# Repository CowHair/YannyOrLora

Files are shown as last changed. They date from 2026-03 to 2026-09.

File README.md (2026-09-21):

# CanSat Competition 2026 Team Yanny or LoRa 🏆 | 1st in Canada 🇨🇦 and represented Canada at the European Space Agency
*From Eric Hamber Secondary School in Vancouver, BC, Canada*

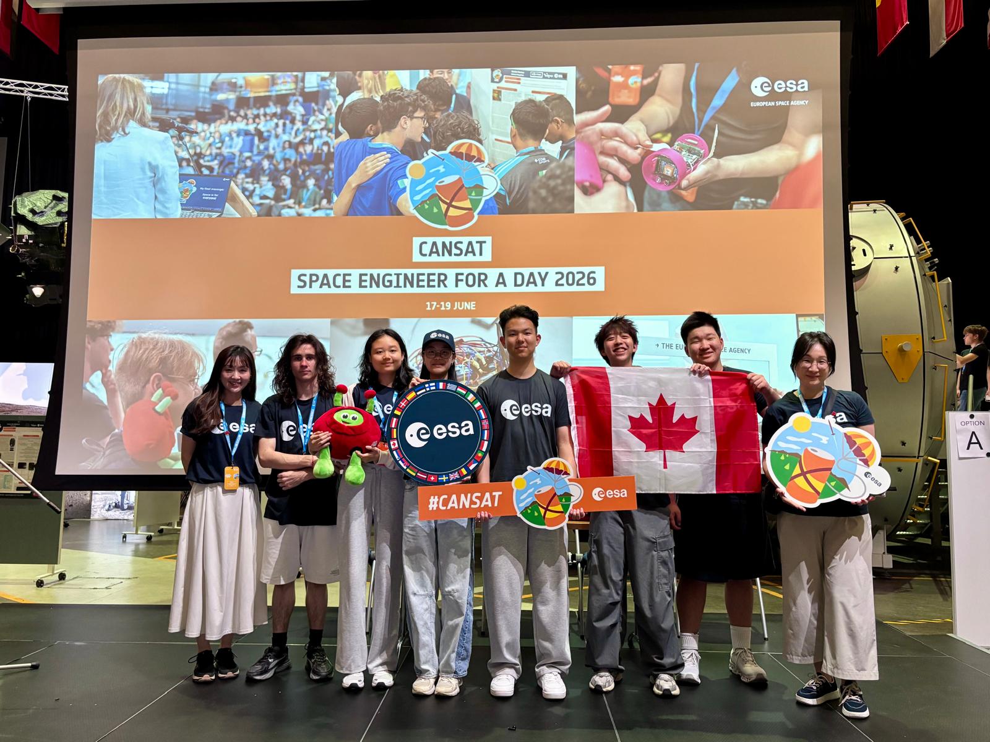
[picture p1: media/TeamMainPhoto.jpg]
Group photo of team


## Team Members

- [Matthew Song](#) - Co-Captain
    - Parachute Design
    - Developing and Testing Landing Gear
- [Asa Liu](#) - Co-Captain
    - Frame Design
    - Mechanical Design
    - Electrical Design
- [Zoey Cheang](https://www.linkedin.com/in/zoey-cheang-855535368/) - Firmware Lead
    - Website Development
    - CanSat Firmware
    - Radio Communication
- [Naiming Zheng](https://www.linkedin.com/in/naiming-z-1a4383371/) - Software Lead
    - Ground Station Software
    - Three-Way Communication Development
- [Bogdan Shkromiuk](https://www.linkedin.com/in/bogdan-shkromiuk-215a08417/) - Hardware Lead
    - Hardware Design
    - CanSat and Radio Device Assembly
    - Frame Design
- [Dora Yuan](https://www.linkedin.com/in/dora-yuan-2a594b307/) - Outreach Lead
    - Outreach Events
    - Designing Landing Gear
    - CanSat Report Main Author

## Project Abstract

The CanSat competition challenges teams to design and build a soda can-sized satellite, launch it to around 1km in altitude, and safely recover telemetry once every second as it descends. Our mission extends the standard telemetry, allowing the CanSat to also act as a relay for a wearable hiker using an SOS device. It listens for signals on a separate radio channel and forwards the hiker's vitals, GPS position, and environmental readings back to the ground station alongside the CanSat's own sensor data, while sending a receipt back to the hiker device so it knows that ground station is aware of its location.

## This Repository

The project is split into the following directories:
 
- [`docs/`](docs/) — our competition website, published live via GitHub Pages at **[https://cowhair.github.io/YannyOrLora]**
- [`firmware/`](firmware/) — Arduino code for all three onboard systems: the CanSat, the ground station, and the SOS device
- [`cad/`](cad/) — 3D models and mechanical design files for the CanSat body and SOS device enclosure
- [`data/`](data/) — telemetry collected during test flights and the competition run
- [`presentations/`](presentations/) — slide decks and reports used during design reviews and the competition

## Mission Overview

The CanSat is launched to around 1km in altitude and descends using a parachute, while continuously transmitting telemetry (temperature, humidity, pressure, altitude, GPS position) to the ground station once per second. Independently, a wearable SOS device carried to simulate a hiker in emergency situation broadcasts a SOS packet with heart rate, GPS position, local temperature/humidity, whenever the button on the device is triggered.

The CanSat acts as the relay between the emergency device and ground station. It listens for the SOS device's signal, caches the most recent emerency data it hears, and piggybacks those fields onto its normal telemetry stream to the ground. The ground station sees both the CanSat's own descent data and the hiker's status in a single feed, without needing separate ground hardware for each link.

## Radio System (Time Sliced Relay Architecture)
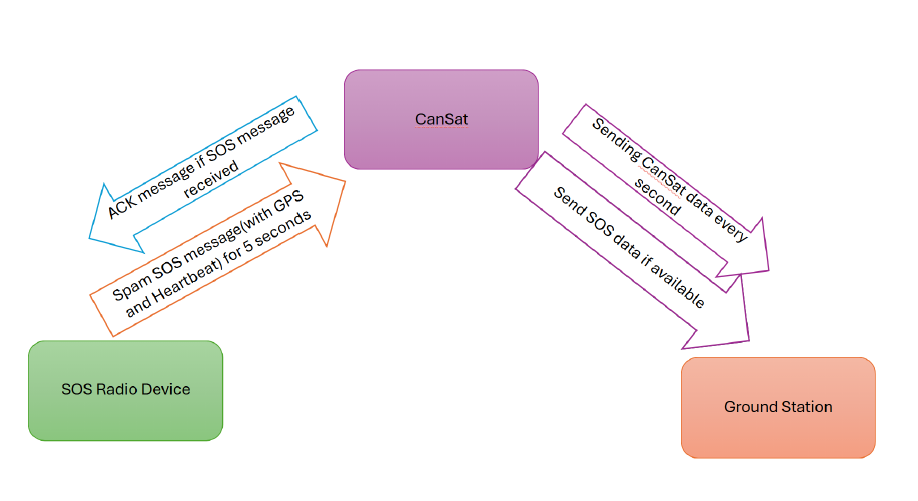
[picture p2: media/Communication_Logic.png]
Communication Logic Image


The onboard radio logic (LoRa, via RadioLib) runs on a strict 1 second frame, split into three phases:

| Phase | Window | Action |
|---|---|---|
| Listen | 0–850 ms | Radio tuned to the SOS device's sync word; any emergency packet received is parsed and cached |
| Transmit | 850 ms–~950 ms | Telemetry is sent to the ground station and an ACK is sent back to the SOS device if time remains in the frame |
| Pad | remainder | GPS and LED housekeeping, holding the frame to exactly 1 second |

Two separate LoRa sync words to keep the two links from colliding on the same channel: one for the CanSat ↔ SOS device link, one for the CanSat → ground link. Cached SOS data expires automatically if no new packet arrives within 10 seconds, so the ground station is never shown stale distress information. ACKs to the SOS device are rate-limited so the CanSat doesn't spend its listen/transmit budget re-acknowledging every frame once contact is established.

## Hardware/Mechanical Design
- Emergency Device Components: BME280, Button, Buzzer, V1 T-Beam ESP32, OLED screen, MAX30102, Toogle Switch, 950kHz Antenna
- CanSat Components: BME280, V1 T-Beam ESP32, LED, Power Switch, 950kHz Antenna
- Designed with FreeCad by Asa Liu and Bogdan Shkromiuk 
<table>
    <tr>
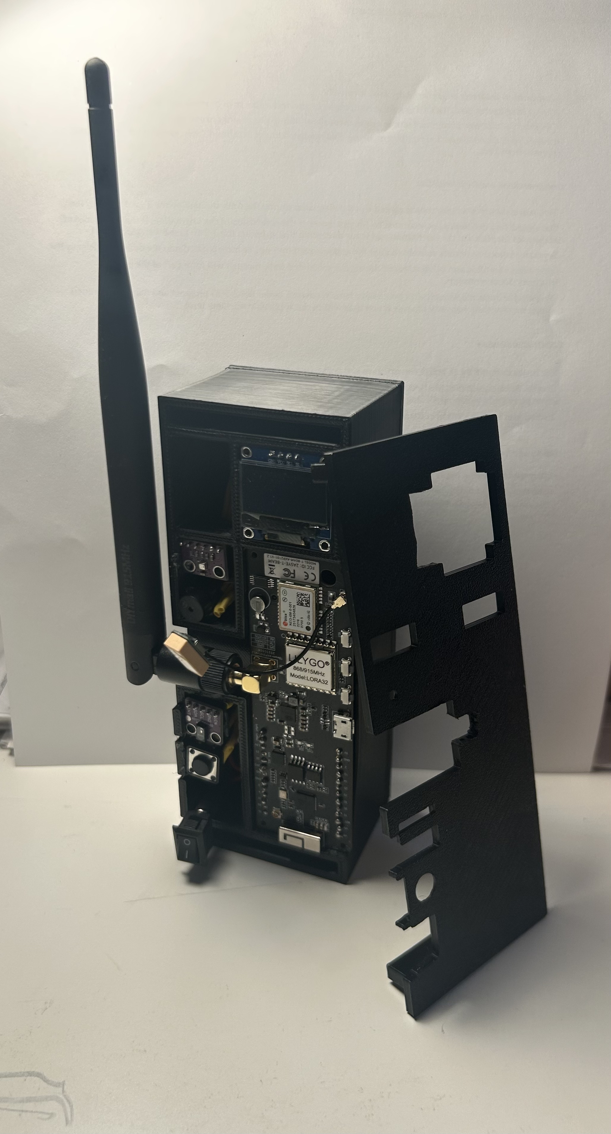
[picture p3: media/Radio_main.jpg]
        <td></td>
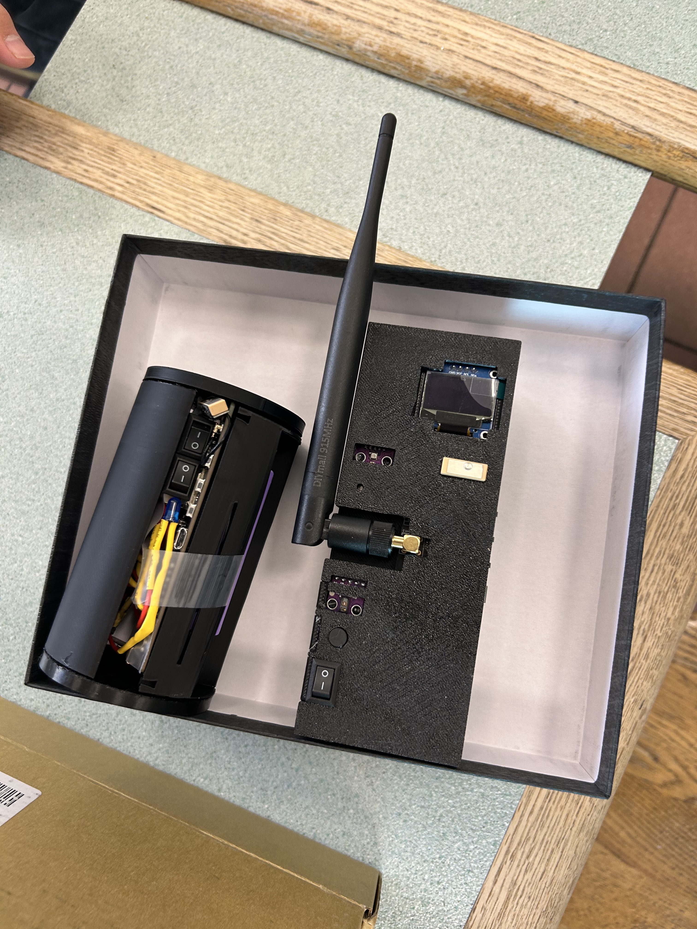
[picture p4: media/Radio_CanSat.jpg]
        <td></td>
    </tr> 
</table>

## Cost Breakdown

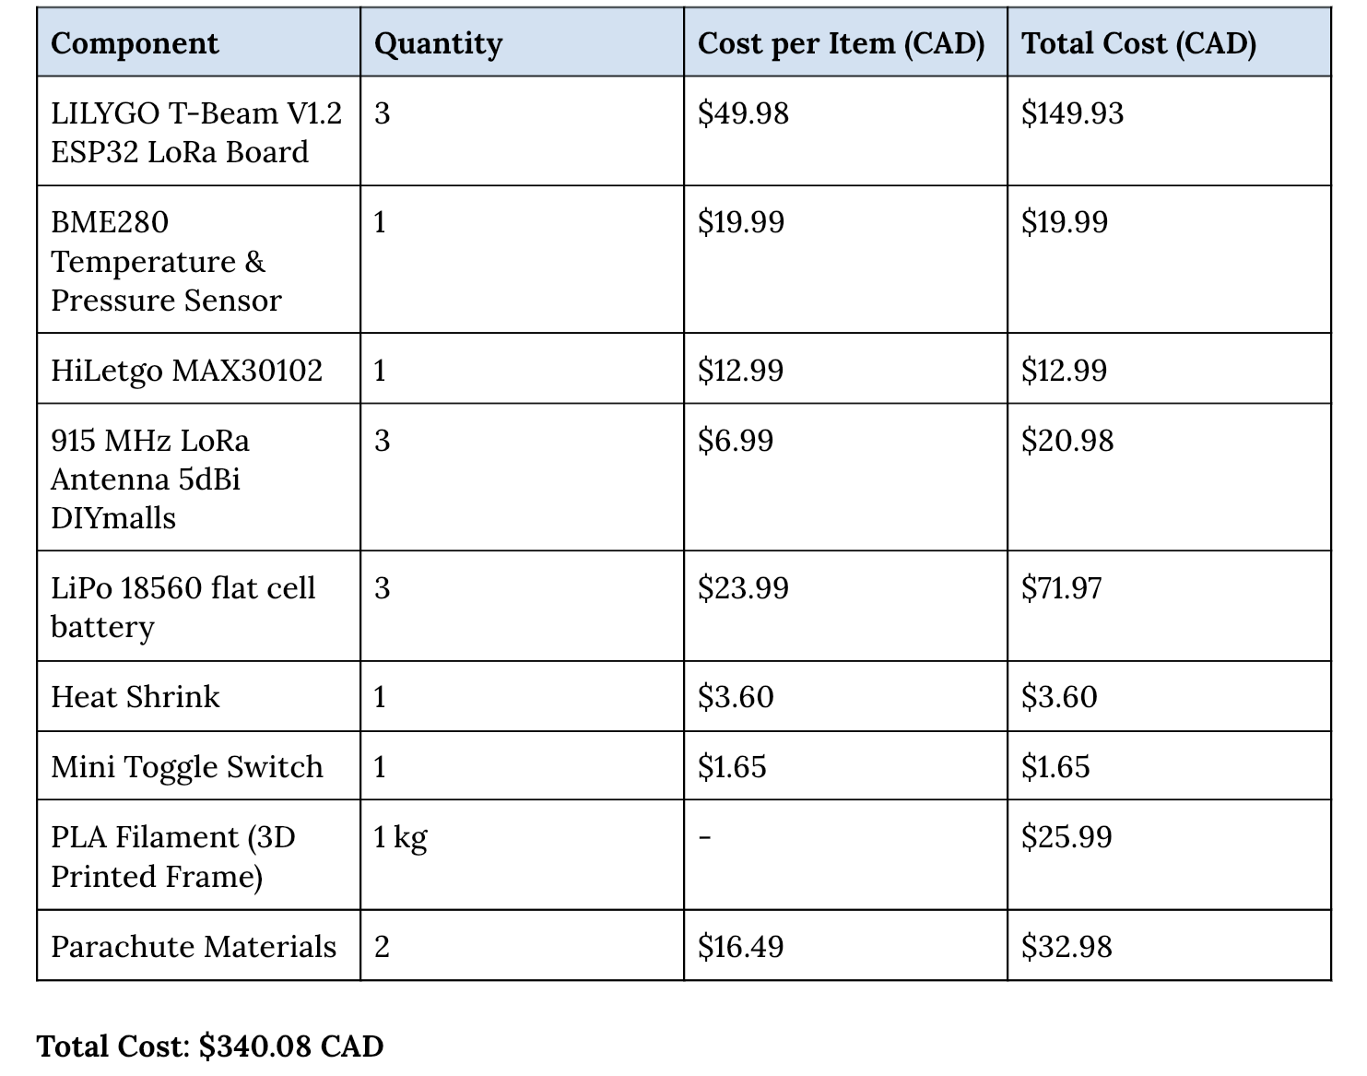
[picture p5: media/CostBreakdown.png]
Table of budget and cost breakdown


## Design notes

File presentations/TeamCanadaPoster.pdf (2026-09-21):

### To measure temperature and pressure once per second

## DESIGN AND COMPONENTS

## PRIMARY MISSION

SECONDARY MISSION To create an SOS radio communication system that includes a hand generator, using the CanSat to extend the range to several kilometers.

## RESULTS

## TESTING

## LESSONS LEARNED

COUNTRY FLAG

# Yanny or LoRa

# CANADA

# CanSat – Space Engineer for a Day 2026

Our CanSat was designed with 3 devices in mind: the ground station, SOS radio device, and the CanSat itself. The LilyGO T-Beam V1.2 ESP32 was chosen as our microcontroller for all 3 devices, for environmental data collection and long-range communication relay.

To build our frames, we used PLA to
maintain a lightweight design for our
CanSat, while our SOS radio device
used nylon as it better protects against external damages. Other components we used includes an OLED display, BME280, and heartbeat sensor on the SOS device to check the user’s health before sending the data to ground station. For our landing system, we used a circular parachute using nylon fabric to prevent ripping during the descent and ensure ease during deployment. Using metal bars and a motor, we also designed a hand crank generator that pairs with our SOS device, ensuring access to the device in remote locations.

After retrieving our CanSat, we noticed water drops from melted snow inside. Fortunately, everything was still functional, and our CanSat did not break.

Our launch conditions were not ideal, with strong winds, a thick cloud cover, and snow. Nonetheless, we successfully received 12 data packets through our LoRa radio system. Halfway through the launch, we lost communication for about 40 seconds and was able to reconnect when it was descending at an altitude of 387.3 metres.

The flight duration was around 150 seconds, the highest recorded altitude reached was 431.7 metres, and the largest distance recorded between the ground station and the CanSat was 599.7m. The descent rate calculated was estimated to be around 5.8m/s. All temperature and pressure data from our BME280 sensor was received successfully in the 12 data packets.

We tested our CanSat extensively, and it was a significant part of our design process.

Firstly, we tested the hardware, including the BME280 sensor, heartbeat clicker, and GPS module. To test, we first had to solder header pins to the LoRa32 board. For some members of our group, it was our first time using Arduino and soldering.

Next, we tested the LoRa communication range by walking in different directions. After confirming a range of around 500–700 meters in dense urban regions with hills, we transferred the BME280 data between the two LoRa32s.

Finally, we tested our parachute landing system using failed frames with weights to find its descent velocity. We walked up a hill and dropped the parachute from 20 meters high. We divided this height by the average time taken for descent to estimate our terminal velocity. To ensure that the parachute would deploy properly under all conditions, we threw it in many different configurations at a variety of linear and rotational speeds.

- The tolerance for PLA has to be a minimum of .25mm and .200 for a perfect fit.
- Designing a PCB would have been a lot for efficient space-wise, removing unnecessary wiring.
- Functionality should be prioritized over aesthetics.

Our secondary mission was very successful. We received 7 packets of data from the SOS radio device, retrieving data on GPS location, temperature, and heart rate.

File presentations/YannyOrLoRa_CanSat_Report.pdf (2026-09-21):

CanSat 2026 | Yanny or LoRa

# Creating an Emergency Radio System Using LoRa Technology

Asa Liu, Matthew Song, Zoey Cheang, Bogdan Shkromiuk, Dora Yuan, Naiming Zheng

Team Name: Yanny or LoRa
School: Eric Hamber Secondary School City: Vancouver, Canada

### ABSTRACT

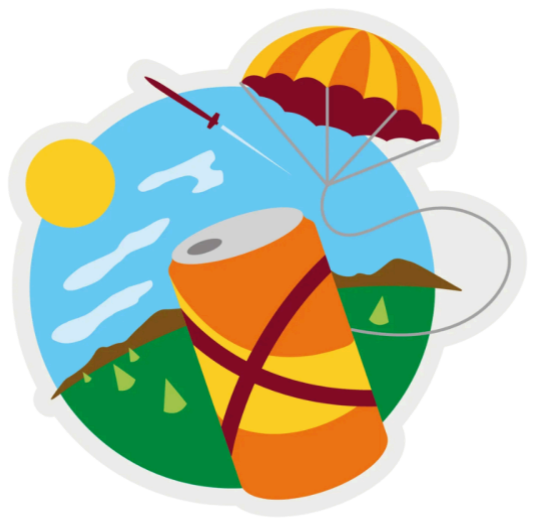
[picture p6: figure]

The advanced CanSat Design Challenge is an annual spring competition where Canadian high school students design a can-sized satellite, which is then launched 1 kilometre by a rocket in Lethbridge, Alberta. Our team, Yanny or LoRa, is composed of 6 high school students from a high school in Vancouver, Canada. Using 3D technology, we constructed a satellite that fulfills two main missions. Our standard primary mission is to collect air pressure, humidity, and temperature data, and to transmit this data through radio back to the ground station. Our secondary mission is to use LoRa (Long Range) technology to create an emergency contact radio system. Our emergency device sends information (specifically SOS signals, heart beat, and GPS location) to the CanSat, which then relays the information back to the ground station. The CanSat allows the message to send through long distances, which we hypothesize to be several kilometres. This store-and-forward system mirrors the communication techniques used in real life satellite systems and is a practical application of aerial LoRa nodes as temporary communication in remote or disaster-affected areas. As the CanSat collects this data, it descends back down using a parachute.

1

### TABLE OF CONTENTS

### 1. INTRODUCTION

### 1.1. Team Mission and Objectives

Our primary mission is to collect air pressure, humidity, and temperature data using a BME280 sensor. This information is collected every second and transmitted through radio to the ground station.

Our secondary mission demonstrates a store-and-forward emergency communication relay system using LoRa radio technology. The concept is that a person in a remote or dangerous location could use a low-power LoRa device to transmit an emergency message to the CanSat, which then relays that message to a home base receiver kilometres away. This has extremely practical effects for a person in a location where they cannot access traditional signal or radio infrastructure. The LoRa technology used for the CanSat extends the effective range of the ground station radio beyond what would otherwise be possible.

Many areas, including Alberta (where we launch our CanSat), have long wildfire seasons that may destroy ground infrastructure and cellular towers. Our CanSat explores the real world problem of finding the minimum viable aerial relay node for emergency communication. Contrary to existing satellites (such as Starlink), our project aims to provide long-range communication without relying on existing infrastructure or

2

large-scale setups. Our aim is to create a useful SOS system that anyone can deploy and use at low cost.

### 1.2. Team Members and Roles

Our team consists of six high school students from Eric Hamber Secondary School, which is a public school in Vancouver, Canada.

Asa Liu (co-captain)
Asa Liu is a grade 11 student at Eric Hamber Secondary who plans on pursuing a future in becoming an astronaut. He has an incredible drive towards building new projects centered around controlled movement. Asa’s background includes many Arduino-based projects and participating in physics competitions. His role in the team is planning and organizing the CanSat build. He is also leading the secondary mission (LoRa development) and designing the frame + hardware systems.

Matthew Song (co-captain)
Matthew Song is a grade 11 student who plans to pursue aerospace or mechanical engineering at university. He has a strong interest in engineering and safety design, and is currently working on an engineering project centered around improving the protective performance of football helmets. Besides academics, he also enjoys golfing and watching football. On the team, Matthew is responsible for developing and testing the landing gear. He will also run meetings and make sure that everyone is on pace to finish.

Zoey Cheang
Zoey Cheang is a grade 12 student who plans on pursuing computer science in university and work in the cybersecurity industry in the future. She has participated in multiple Capture The Flag competitions and is working toward building a strong foundation in networking protocols. She is comfortable coding with Python, C++ and Java. Zoey will be focusing on working on the three-way communication LoRa protocol, electronics hardware, and creating a website for the team.

Naiming Zheng
Naiming Zheng is a grade 11 student at Eric Hamber Secondary School who plans to pursue computer science at university. He is proficient in Python and Java, and he is currently trying to learn Rust to get a deeper understanding of system programming and memory safety. Naiming is also in Eric Hamber’s cybersecurity club and competes in Capture the Flag Competitions. Naiming is responsible for the software side of the primary mission, focusing on sensor data processing and controller logic.

3

Dora Yuan
Dora Yuan is a grade 11 student at Eric Hamber who is passionate about engineering, and is planning on pursuing it in university. She has a strong background in physics, is proficient in Python, and is currently expanding her knowledge on electronics and CAD. On the team, she will be leading the outreach, as well as working on the CanSat landing gear. She is the main writer of this report.

Bogdan Shkromiuk
Bogdan Shkromiuk is a grade 12 student at Eric Hamber who plans to pursue electronic engineering at university. He has a strong physics background and is experienced with 3D modeling, printing, and soldering. He will use these skills to build the CanSat frame and help with electronics.

TEACHER: Mark Lam
Mark Lam is this team’s teacher and an Eric Hamber alumnus who graduated from UBC with a degree in physics. At Eric Hamber Secondary, he teaches many physics courses, including both AP Physics C classes. He has been doing CanSat with his students for many years, on top of supporting his class in various other physics events and opportunities.

### 2. CANSAT DESCRIPTION

### 2.1. Mission Overview (Main Components)

LilyGO T-Beam V1.2
Figure 1: LilyGO T-Beam

4

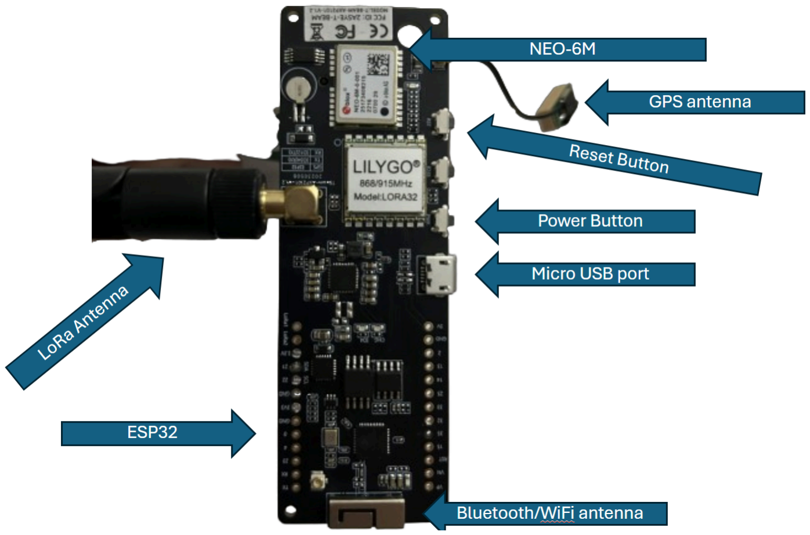
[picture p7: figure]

There are three main devices in our missions, CanSat, ground station, and SOS radio device. Our central component for all three devices is a LilyGO T-Beam V1.2. This contains a microcontroller, a LoRa module, a GPS module, an antenna, and a built-in battery connector.

Microcontroller
The microcontroller we are using is an ESP32. The board is mounted in the middle platform of the CanSat structure using plastic layers and screws. We have also used standoffs to prevent electrical contact between circuit board and base to prevent electrical short circuits.

LoRa Module
The LoRa module we are using is SX1276. It is designed specifically for long range, low-powered wireless communication, which greatly suits our missions. In our missions, it will be operated in the 915MHz ISM band.

GPS module
We are using the u-box NEO-6M GPS module. It provides geographic coordinates and altitude, helping us to track the CanSat location.

Antenna
We are using a 915 MHz LoRa antenna to match the frequency we are using for our LoRa transmitter. The antenna is mounted with the SMA male of the T-Beam module.

Battery
We will be using the LiPo 18650 flat-top cell 3.7V battery. It provides enough voltage to power the ESP32 and other sensors. The battery is housed in the integrated holder on the underside of the T-Beam. It is rechargeable via the micro-USB port integrated directly onto the T-Beam board.

CanSat
The main parts of our CanSat consists of a LilyGO T-Beam V1.2 mentioned above, a LED, a sensor, a power switch, and a parachute.

Figure 2: Our CanSat

5

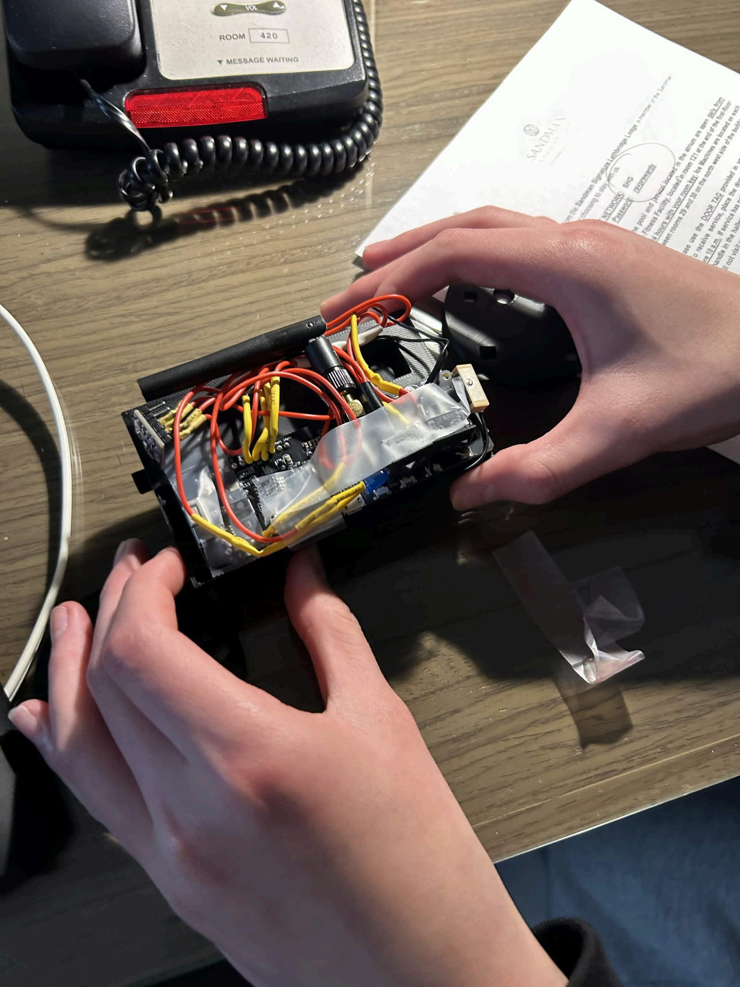
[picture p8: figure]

Sensor
We are using a BME280 sensor, which tracks temperature, air pressure, and humidity. The sensors will be mounted on the same platform as the microcontroller. There will be holes to allow for air to flow in without endangering the sensor.

LED
The LED is used as an indicator when the CanSat is powered on. It is clearly visible on the side of our CanSat.

Power Switch
The power switch is clearly visible on the side of our CanSat, alongside with the LED to power on the CanSat.

Parachute
Our circular parachute system is attached to the top of the CanSat structure. The attachment point is reinforced to withstand the forces experienced when the parachute deploys. The parachute lines connect to the top cap so that the CanSat remains upright during descent, ensuring the antenna maintains good communication with the ground station. More information about the parachute can be found below, in 2.5. Recovery System.

SOS radio device

6

The main components of our SOS radio device consists of a BME280, a heartbeat sensor, a buzzer, a power switch, a LilyGO T-Beam V.1.2 (mentioned above), SOS button, and an OLED screen.

Figure 3: Radio device

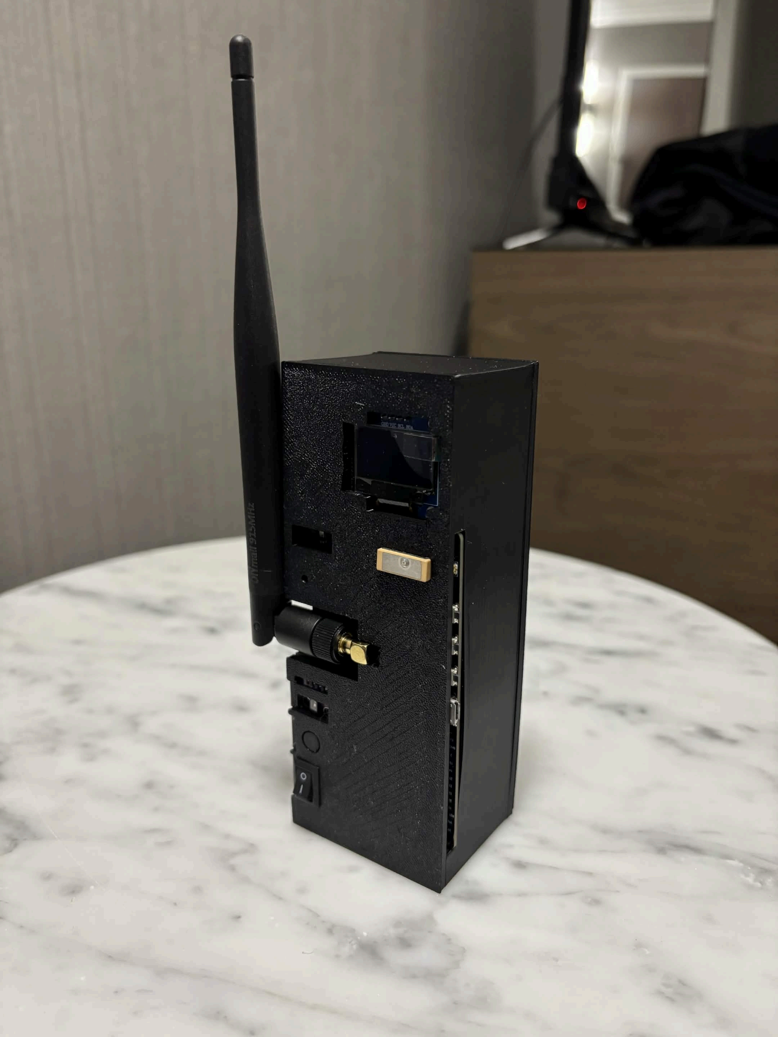
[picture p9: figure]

OLED Screen
The OLED screen displays BME280 data (Altitude, Humidity, Pressure, Temperature), GPS location, and heartbeat (in BPM). When an SOS message is sent, the OLED screen will indicate to the user that the message is being sent. When the SOS radio device receives an ACK message from the CanSat, the OLED screen will display to the user that the message is sent successfully.

BME280
The BME280 sensor allows us to collect temperature, humidity, altitude, and air pressure allowing the ground station to see the surrounding conditions of the SOS Radio.

Heartbeat Sensor
Using a simplistic 3d frame design we are able to collect the heart rate (bpm) of any user that puts their finger on top of the carefully designed frame that rests on top of the sensor. When measuring your heart rate the OLED screen automatically switches to heart reading mode and displays your bpm in big visible numbers.

LILYGO T-Beam v1.2
The LoRa32 microcontroller is the core of the SOS device. It is connected to all the parts and processes both sensors while communicating with the CanSat.

Buzzer

7

The buzzer beats to the BPM and is only active when a finger is on the sensor.

Power Switch
Turns on/off the SOS Radio.

SOS Button
Sends an SOS signal to the CanSat when double-clicked. Double-clicking again cancels the SOS. Sends the GPS location and the heartbeat of the radio device user.

### 2.2. Structural Design (Frame)

For the final frame design, we went with a 4-part frame with 2 body parts along with a top lid and bottom lid.

Figure 4: Frame

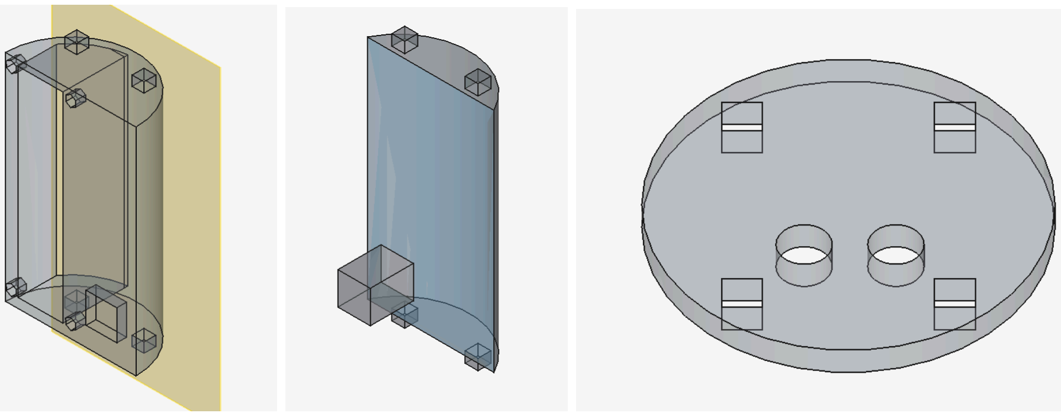
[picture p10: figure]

The diameter of the frame is exactly 66mm, and the height of the CanSat is 115mm (105mm body and 5mm lids). The interior design had to fit the 65mm LoRa32 + antenna, so we chose not to add walls on the side but instead reinforce it using the top and bottom. This also allowed for easy placement of switch, LED, and antenna holes.
The top lid includes a hole for the GPS to reach open sky while the bottom lid includes a circular hole for air to reach the BME280. Inside the body, we implemented 4 screw holes to tightly secure the LoRa32 to the frame.
Finally two holes were implemented on the top for parachute connection. We made sure the top lid was tightly sealed on the CanSat body so that it wouldn't fly off during parachute activation.

### 2.3. Electrical Design

Figure 5: SOS radio device wiring

8

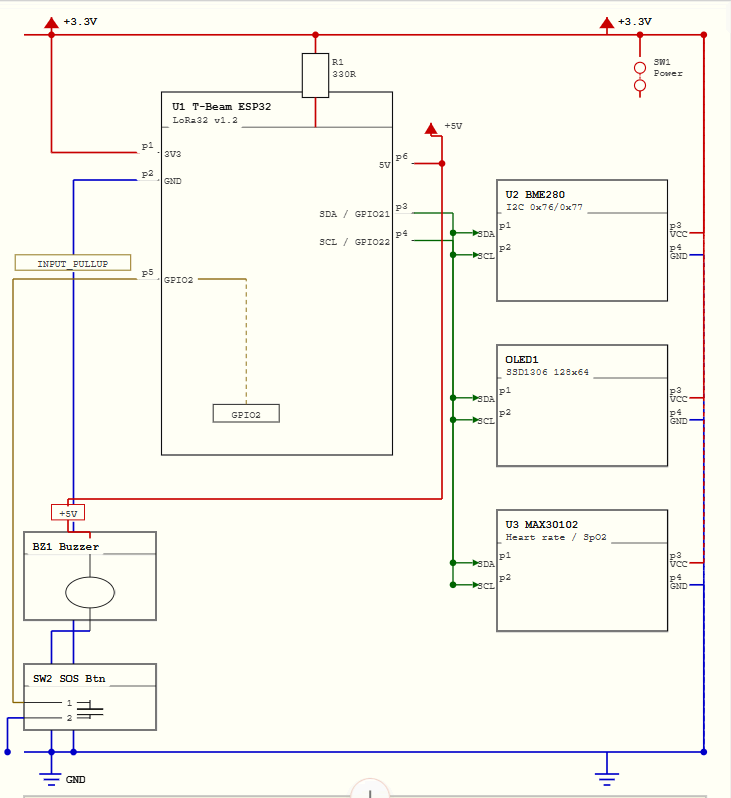
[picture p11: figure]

BME 280
- Uses I2C (SDA=GPIO21, SCL=GPIO22)
- Connected to 3.3V and GND
OLED screen
- Uses I2C (SDA=GPIO21, SCL=GPIO22)
- Connected to 3.3V and GND MAX30102
- Uses I2C (SDA=GPIO21, SCL=GPIO22)
- Connected to 3.3V and GND Buzzer
- Connected to 5V and GND
SOS button
- Connected to GPIO2 (INPUT_PULLUP) and GND Toggle switch
- Connected in series with BME280 and 3.3V

Figure 6: CanSat device wiring

9

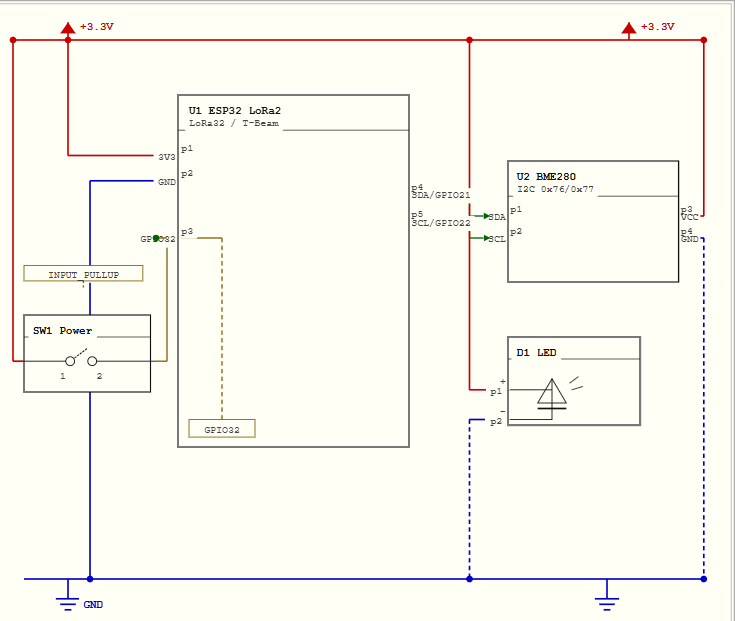
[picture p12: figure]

BME280
- Uses I2C (SDA=GPIO21, SCL=GPIO22)
- Connected to 3.3V and GND
LED
- Connected from 3.3V to GND so it turns on while the LoRa32 is on Toggle switch
- Connected between GND and GPIO32
Input Pullup
- Acts as an internal resistor to bring down voltage to 3.3V Battery
- Powers everything

### 2.4. Software Design

Figure 7: Communication Logic

10

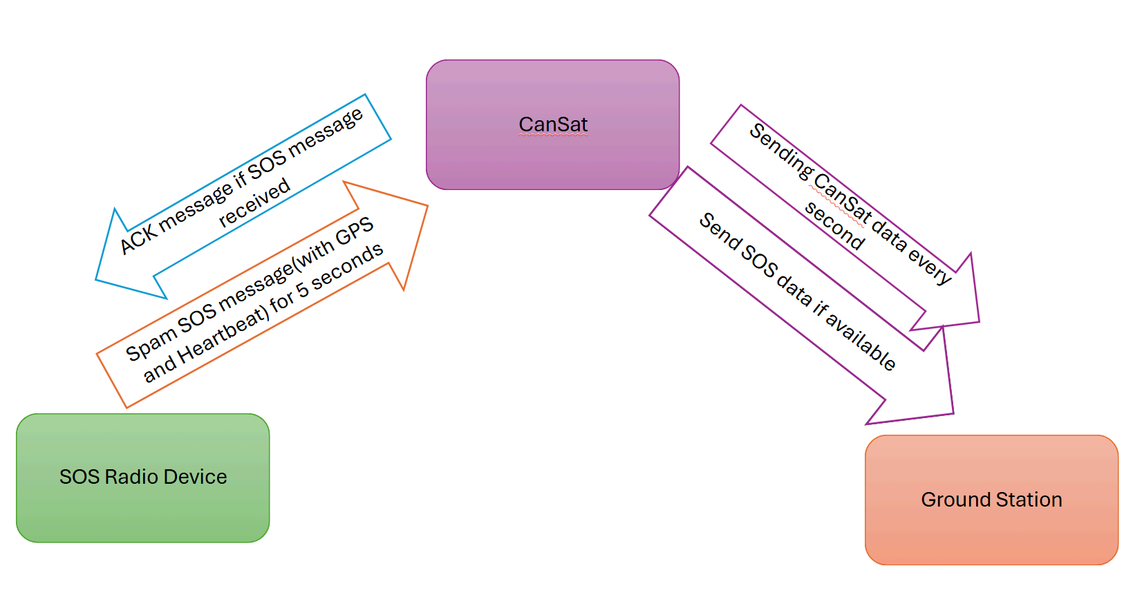
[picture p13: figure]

Our secondary mission uses three-way communication to communicate between the SOS radio device, CanSat, and the ground station. Since LoRa is not able to receive (RX) and send data (TX) at the same time, the CanSat would have to alternate between RX and TX mode to communicate with both the ground station and the SOS radio device. With the primary mission requirement, we are required to send CanSat data to the ground station every second. In another word, the CanSat will have to alternate between RX and TX mode within one second. To ensure the SOS message is successfully received by the CanSat, we use the following logic:

### 1. The SOS radio device spams an SOS message to the CanSat for 5 seconds, then

immediately changes to RX mode.
2. The CanSat is in RX mode for around 0–850ms.
3. The CanSat is in TX mode at around 850–910ms. (Relaying SOS message if available, and sending CanSat data to the ground station)

### 4. The CanSat sends an ACK message (acknowledgment message) to the SOS radio

device after successfully receiving the message.
5. The CanSat is in TX mode (ACK if available) at around 910—925ms.

### 6. The SOS OLED screen displays that the message is successfully received by the

CanSat.

### 7. If the SOS radio device does not receive an ACK message from CanSat, the SOS

message is spammed again for 5 seconds to the CanSat.
Using the logic above, the CanSat is in RX mode 80% of the time, ensuring the SOS data is successfully received and relaying back to the ground station.

Figure 8: Dashboard

11

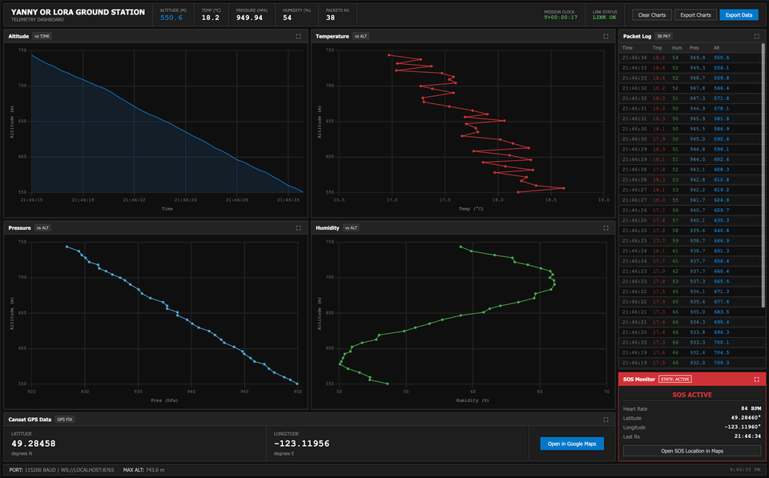
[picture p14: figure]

Our dashboard, which is at the ground station, features several information:

1. An altitude vs time graph 2. An altitude vs temperature graph 3. An altitude vs air pressure graph 4. An altitude vs humidity graph 5. The GPS, temperature, pressure, and humidity data of the CanSat 6. The GPS coordinates of the emergency device (in longitudes and latitudes) 7. An SOS message monitor, which alerts when an SOS signal is received

Our dashboard makes it so that it is easy to search up the GPS coordinates on Google Maps. We originally wanted to include a static map within the dashboard itself, but we couldn’t obtain a license to download one in time. For future prototypes, we hope to be able to include a map. The dashboard is created in HTML and using python and javascript, we are able to connect to the ground station serial monitor to display the data in our dashboard.

### 2.5. Recovery System

Our recovery system is a parachute to slow down the CanSat’s descent. Our parachute is made of nylon fabric. It has a diameter of 0.4 m, but there is a hole in the middle with a diameter of 0.12 m, so the area of the parachute is 0.114m². After the CanSat is launched, the parachute allows it to generate drag force as it descends back down. Drag force is described by the following:

F | ,
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
Where ρ is air density, v is descent velocity, C is the drag coefficient, and is the area of
d

A
the parachute. At terminal velocity, drag force is equal to the gravitational force on the CanSat (mg). According to our research, circular parachutes have a drag coefficient of approximately 1.75, but since there is a hole in the middle of ours, we assume that our drag coefficient will be 0.8. The density of air at sea level is approximately 1.229 .

kg
m

3

At terminal velocity, the net force is 0. Since the two forces acting on the parachute are drag force and gravity, the terminal velocity of the parachute can be calculated:
F

D = F
g
1
2

ρv

2
C
d

A = mg

v | ,
T =

2mg
ρC
d

A
Where v is the terminal velocity in , g is 9.8 , and m is the mass of the CanSat, which
T

m
s

m
s

2
is 0.301 kg. By plugging in our numbers:
v | .
T =

2(0.301)(9.8)
(1.229)(0.8)(0.114) = 7. 24

m
s

Our approximate terminal velocity 7.24 , which is within the required descent velocity.

m
s

Our initial design for the parachute was made using plastic garbage bags, which we chose for its light weight and ability to deploy reliably. However, during testing, the material was found to be too fragile, as the parachute tore upon impact with a tree. In this initial configuration, the parachute had a diameter of 140 cm and produced an estimated descent rate of 2 m/s, which was well under the recommended minimum velocity. Consequently, a second design was developed using nylon fiber, which was strong enough to not rip during the launch or descent. For the revised parachute, the diameter was reduced to 40 cm, resulting in an increased descent rate of approximately 4 m/s, which significantly reduced the horizontal drift. However, upon arrival in Alberta, we realized that the wind speeds were approximately 50 km/h, which would drift the CanSat more than 5 km away from the launch point. To address this issue, a 12 cm diameter vent was added to the centre of the parachute. The estimated increase in descent rate would keep the parachute within a reasonable distance from the launch site, while still keeping it within the maximum recommended speed from the rulebook.

The string that attaches to the CanSat is evenly spread out across the edge of the parachute, connected at 8 points to make sure the parachute is symmetrical. The string is

13 made of polypropylene twine; one of the requirements is that it had to withstand 30 Newtons of force, and we found this to be the strongest option. Unlike the braided fishing line, which we also considered, the polypropylene twine did not tangle as easily.

Figure 9: Parachute

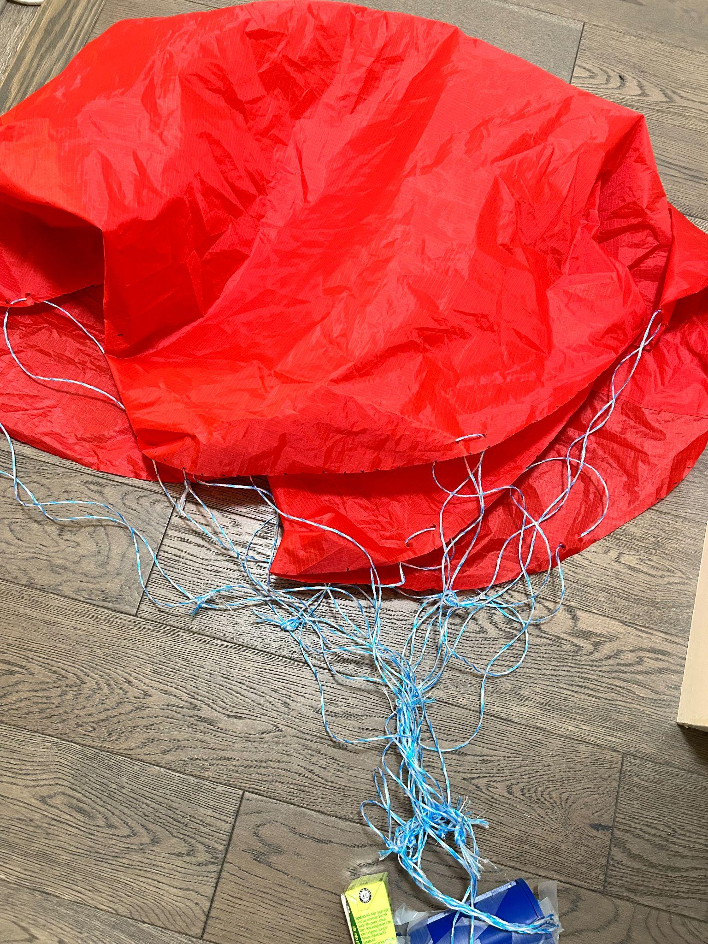
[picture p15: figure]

### 3. PROJECT PLANNING

### 3.1. Budget

Table 1: Budget
Component | Quantity | Cost per Item (CAD) | Total Cost (CAD)
LILYGO T-Beam V1.2 ESP32 LoRa Board | 3 | $49.98 | $149.93
BME280 Temperature & Pressure Sensor | 1 | $19.99 | $19.99
HiLetgo MAX30102 | 1 | $12.99 | $12.99
915 MHz LoRa Antenna 5dBi DIYmalls | 3 | $6.99 | $20.98
LiPo 18560 flat cell battery | 3 | $23.99 | $71.97

14

Component | Quantity | Cost per Item (CAD) | Total Cost (CAD)
Heat Shrink | 1 | $3.60 | $3.60
Mini Toggle Switch | 1 | $1.65 | $1.65
PLA Filament (3D Printed Frame) | 1 kg | - | $25.99
Parachute Materials | 2 | $16.49 | $32.98

Total Cost: $340.08 CAD

### 3.2. Testing Process

Our testing process took the majority of the time, and started after we got our parts.

The first test was the hardware testing where we tested the BME280 sensor, heartbeat clicker, and GPS module. For some members of our group, it was the first time using Arduino and soldering, so we all took time learning it. To test them, we first had to solder header pins to the LoRa32 board.

After, we tested the communication for the LoRa and walked in different directions to test its range. After confirming a range of around 500–700 metres in dense urban regions with hills, we transferred the BME280 data between the two LoRa32s.

The third step was to fully wire the SOS system and the CanSat system to see how each part interacted with each other. At this time, we also began designing the frame and parachutes.

When we finished breadboarding and tested each device individually and in pairs, we split into 4 teams. One team would solder the wires together, one team would work on the parachute, one team would 3D design the frame, and the last team to finish the 3-way communication code.

After the parachute was finished, we began using our failed frames with weights to test its falling velocity. We walked up a hill and dropped the parachute from 10 meters high. We divided the distance, which was 10 meters, by the average time taken for descent to find the descent velocity. To ensure that the parachute opened under any circumstance we threw it in many different configurations at a variety of linear and rotational speeds.

15

Once the frame was finalized, we tested its energy dissipation capabilities by dropping it against the floor at different heights and measuring the total energy before and after its collision with the ground. These tests ensured that we had a frame that best protected the components inside during both the launch and the impact with the ground after descent. This was necessary considering the potential 20 g’s of force the CanSat may endure.

When everything was soldered, we could finally test the 3-way communication. This proved to be incredibly hard and took a long time to get working, because the CanSat could only either receive or send signals, not at the same time. During the testing, we also started placing components in the SOS radio frame and CanSat frame along with the parachute.

Finally, we finished all the testing and sealed the lid one last time. We learned that instead of using a breadboard and headerpins, we should have used a custom PCB and solder directly because it would have saved hours of unsoldering and rewiring. We originally had a separate battery, but the LoRa32 came with a built-in battery holder and we had difficulties unsoldering the original. This made creating the frame incredibly difficult, because we had to keep remaking it.

### 4. OUTREACH PROGRAM

Our outreach program consisted of both social media and in person presentations.

For social media, we made a website to explain our project, as well as an Instagram page that regularly updated with stories and posts to illustrate our process. Our Instagram has several hundred followers.

Table 2: Summary of social media activities
Platform | Link | Description
Website | https://yannyorlora.tech | CanSat information + mission homepage
Instagram | https://www.instagram.com/yannyorlora (https://www.instagram.com/yannyorlora?igsh=MWRwYmxwdGRsZ2w0aw==) | Work-in-progress updates (on our story), informative posts, record of in-person outreach activities
LinkTree | https://linktr.ee/yannyor lora (https://linktr.ee/yannyorlora) | Central hub for social media information

16

For our in person outreach, we gave three presentations to various audiences. The first presentation was done to a high school audience, in a STEM-focused school club called Experiment Club. This audience (grade 8–12) was very fitting because participants were already interested in science and engineering. Our presentation focused on explaining what CanSat is, as well as running an activity on circuits and breadboards. We taught students how to use breadboards to create several types of circuits, using LEDs. We then explained how we use solderless breadboards to help us test the CanSat in its design stage. Several of our participants expressed interest in the CanSat competition.

Our second in person presentation was given to an elementary school audience, to a grade

### 4 class in a public elementary school called Quilchena Elementary. We talked about our

CanSat to the class, and then ran an egg drop activity. During our time there we spoke with some individuals with incredible talent with the same catchment as our school so we hope to see them participate in CanSat in the future.

Our third in person presentation was given to a public audience at our local community centre, called Kerrisdale Community Centre. We gave our presentation to a class of kids aged 9-12 in a STEM program (this is a public program that allows both registration and drop-in). We presented our CanSat, and then ran an egg drop activity.

Figure 10: Pictures from our in person outreach events

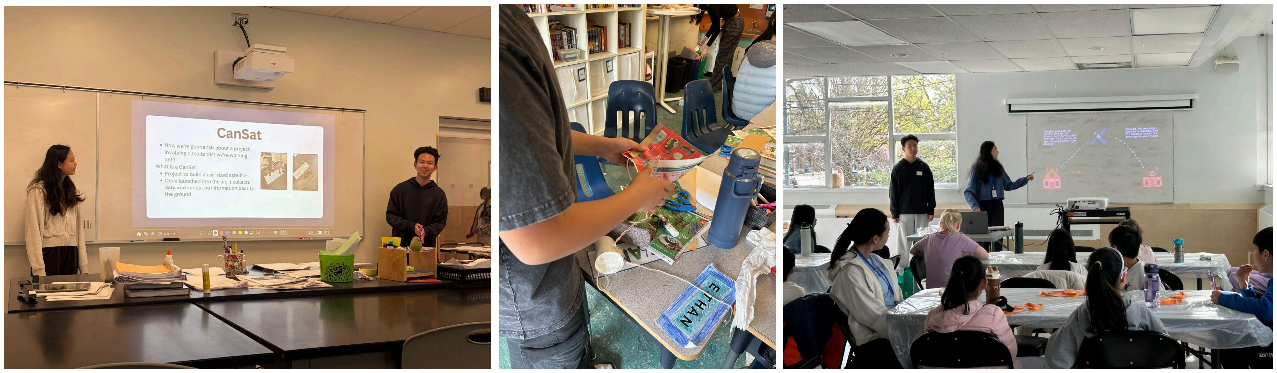
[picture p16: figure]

### 5. APPENDIX: FRAME DESIGN PROCESS

The goal of our frame design was to develop a casing that fit the 66mm x 115mm size while leaving room for the LoRa32 and antenna. It also had to fit all the parts in a secure way so that on the launch up and during the descent the parts wouldn’t be moving around. The

17 launch force was estimated to be 20gs and the landing speed was estimated to be around 7m/s. This was our basis before designing the frame.

The material we used during printing was PLA, and the software used for the design is FreeCAD. Below are some drafts we made during the design process.

Draft 1 (Unfinished)

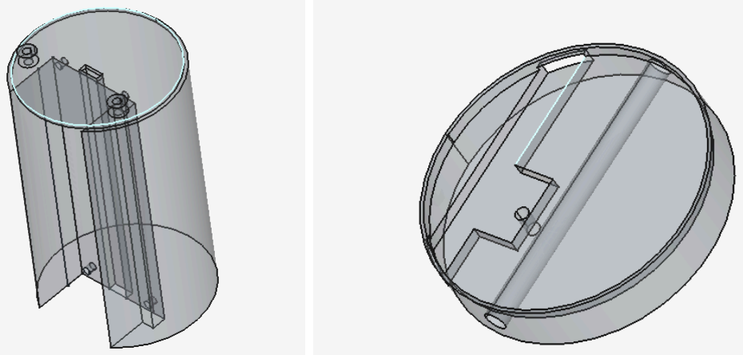
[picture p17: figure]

The idea was to have half the circle be 3D printed so that we could change the weight to counter the battery and LoRa32 weight. It had a cut-out hole and screw holes to secure the microcontroller. This was our first time 3D designing.

Missing: proper dimensions, LED hole, charger hole, battery hole, switch hole, parachute holder.

Draft 2 (unfinished)

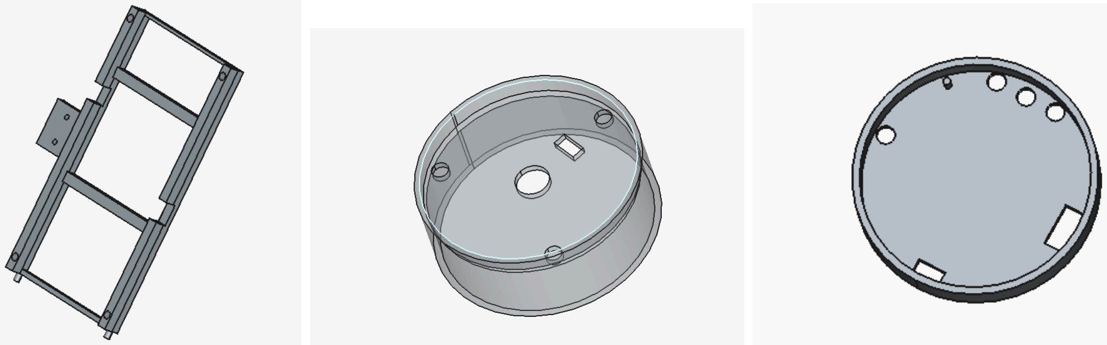
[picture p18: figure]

This was completely different from the original design. We printed a standalone middle frame to act as a slide holder for the LoRa32. This design left space for wiring and components to be on the side. The middle standalone frame also included screw holes for

18 the CanSat and a side platform for the BME280 sensor. There were 3 holes on the bottom frame to allow air to reach the sensor.

Missing: proper battery holder, side walls to protect the centre, incorrect charger placement.

Draft 3 (unfinished)

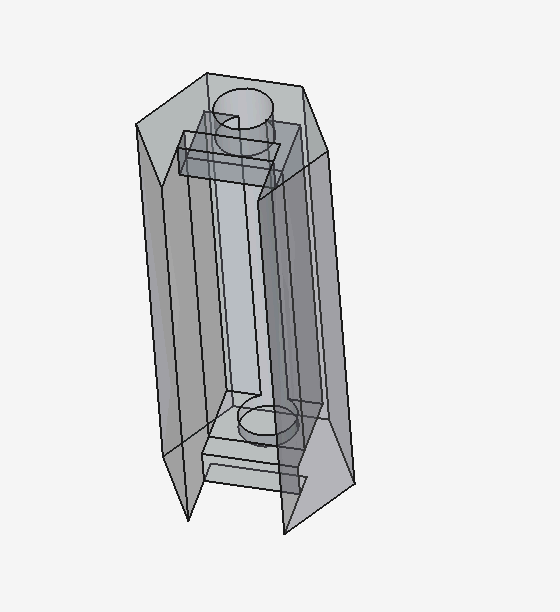
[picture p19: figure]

For this design we tried something new: a single piece design with a sliding door for battery access and an antenna channel through the centre of the body along with mounting bars for the top and bottom. For this design, the BME280 sensor was planned to be taped to the interior side of the wall.

Missing: charging hole, parachute holder

Draft 4

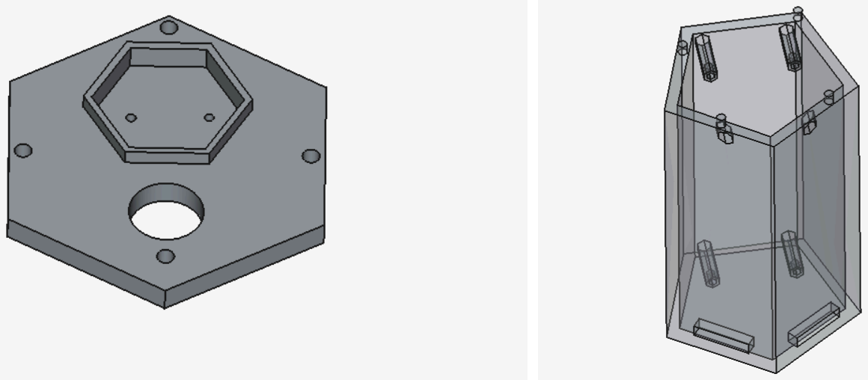
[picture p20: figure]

This was the most complete design so far. Changes included a pentagon body shape which allowed for flat faces on the sides making it easier to mount hardware and add features compared to a circular body. There are 4 pegs to mount the LoRa32 while leaving space behind for battery and wiring. Air vents were also added to let in air for more precise readings. The top lid was designed to have an antenna hole and a parachute holder with 3 secure holes to allow for parachute knotting.

19

Missing: BME280 mounting area, charging hole, battery switch hole, antenna mount

Draft 5

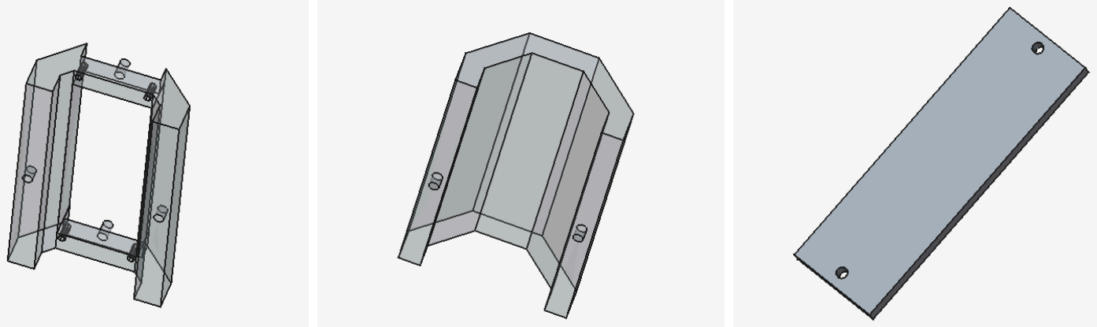
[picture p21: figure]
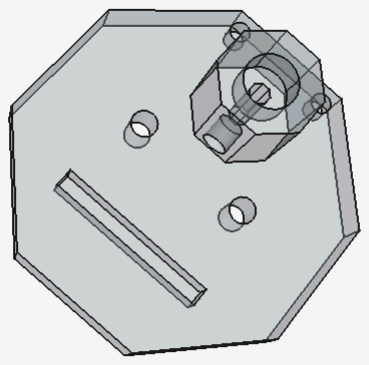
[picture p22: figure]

This was the first complete design with all the proper parts to secure the components. This had a 4 part system where the two body parts would snap together before securing the top lid and bottom lid (no image) sandwiching the body. This was a massive improvement as it left space for battery change and had a dedicated antenna holder and a case to close the battery. After printing, many flaws were found, such as wrong sizes for the antenna hole and battery holder. Securing pegs were also too small and often snapped.

Missing: proper measurements.

Version 6 (Final Version)

More information about this frame can be found in 2.2. Structural Design (Frame).

During our testing, we discovered that the antenna had to be connected to the SX1276 dedicated SMA port on the board, and we did not have an extension. This meant that the board and antenna would be exactly 65mm, which was a problem. Instead, we ditched the side walls and focused the strength on the top and bottom.

20

In our design, we have a place to screw the LoRa onto the body with an open battery holder to hold and change the battery without taking it apart. The right side of the body was left for the antenna, and the extra room on the bottom left was used as extra security. The top and bottom frame were nearly identical except for a small hole for the GPS module.

This design worked well, but the wiring we used was too big and it took a while to fit everything together. The best part about this design was that it allowed lots of room on the side for the switch, LED, charger port, and sensor.

The main lessons we learned from this design process are the following:
1. Tolerance: had to be at least .25mm and .200 for perfect fit PLA.

### 2. Pre-planning: If we were to design it again, planning out where all the components

should be placed first would allow us to be more efficient. PCB designing would have also saved us a lot more space rather than tons of wiring.

### 3. Functionality: For the second and third design, we tried to make it look more

aesthetic, but it was not actually practical. We learned functionality should be prioritized.

21

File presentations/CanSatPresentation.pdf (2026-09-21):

# YANNY OR LORA

CanSat 2026 | April 2026

# CREATING AN EMERGENCY RADIO SYSTEM USING LORA TECHNOLOGY

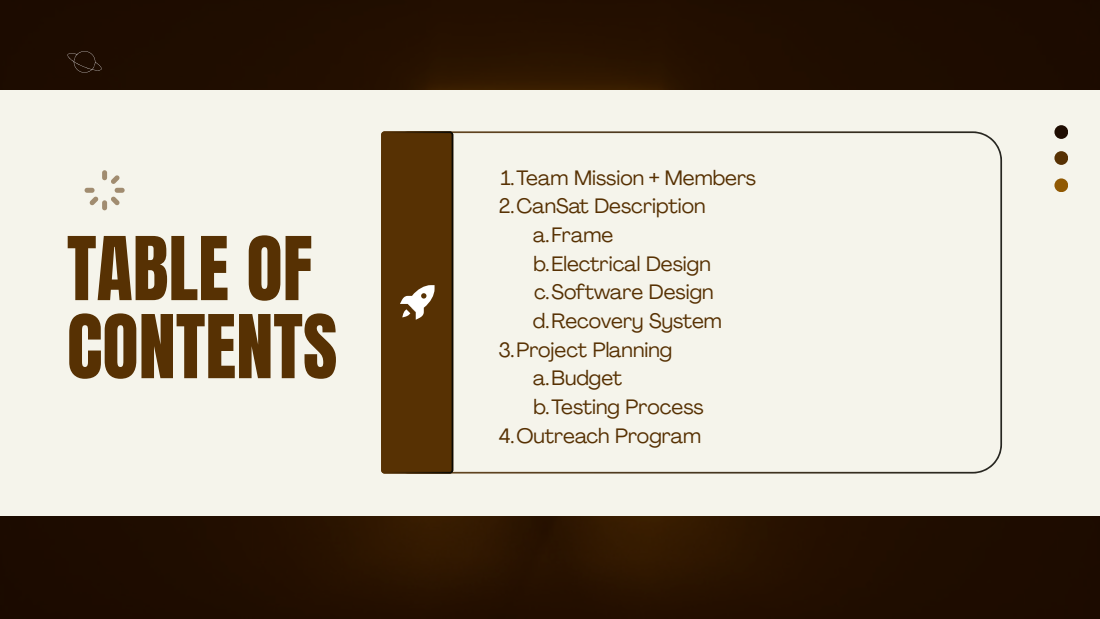
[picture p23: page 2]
TABLE OF CONTENTS

1.Team Mission + Members
2.CanSat Description
a.Frame
b.Electrical Design
c.Software Design
d.Recovery System
3.Project Planning
a.Budget
b.Testing Process
4.Outreach Program

# WHO WE ARE

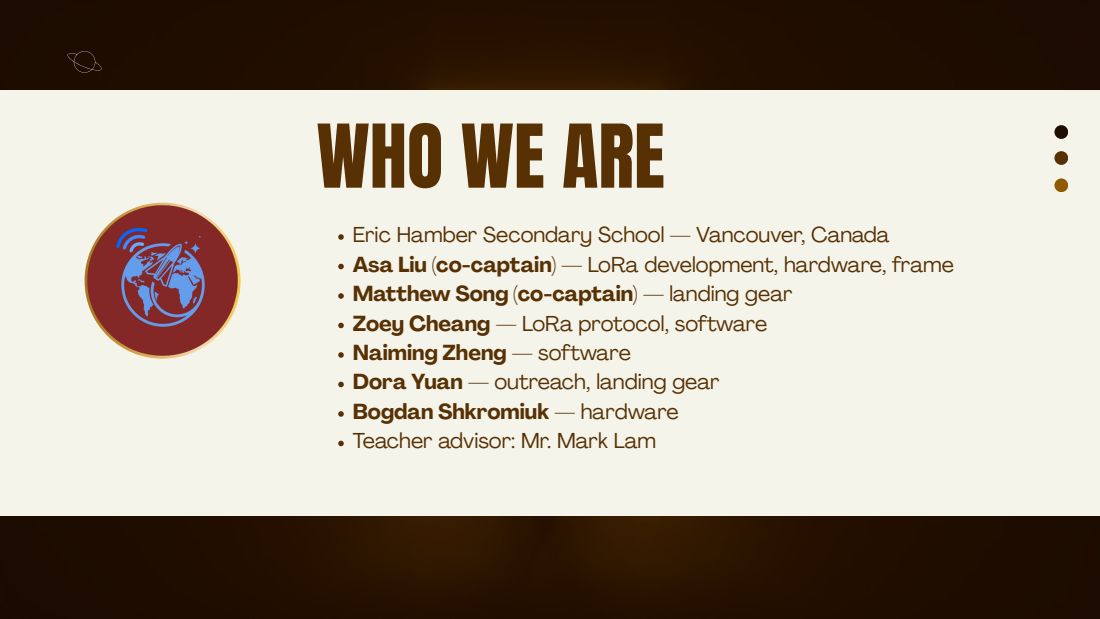
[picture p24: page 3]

Eric Hamber Secondary School — Vancouver, Canada
Asa Liu (co-captain) — LoRa development, hardware, frame
Matthew Song (co-captain) — landing gear
Zoey Cheang — LoRa protocol, software
Naiming Zheng — software
Dora Yuan — outreach, landing gear
Bogdan Shkromiuk — hardware
Teacher advisor: Mr. Mark Lam

# THE PROBLEM

Many areas, like BC (where we’re from) and Alberta (here!) can have long wildfire seasons Wildfires, floods, and natural disasters destroy cell towers and ground infrastructure Hikers and people in remote areas have no reliable communication
Existing solutions (Starlink) cost $600+ and require setup — not viable in emergencies Ground-level radios have limited range
Our question: how to develop an emergency communication system that anyone can easily deploy, without spending $$$ or relying on existing infrastructure?

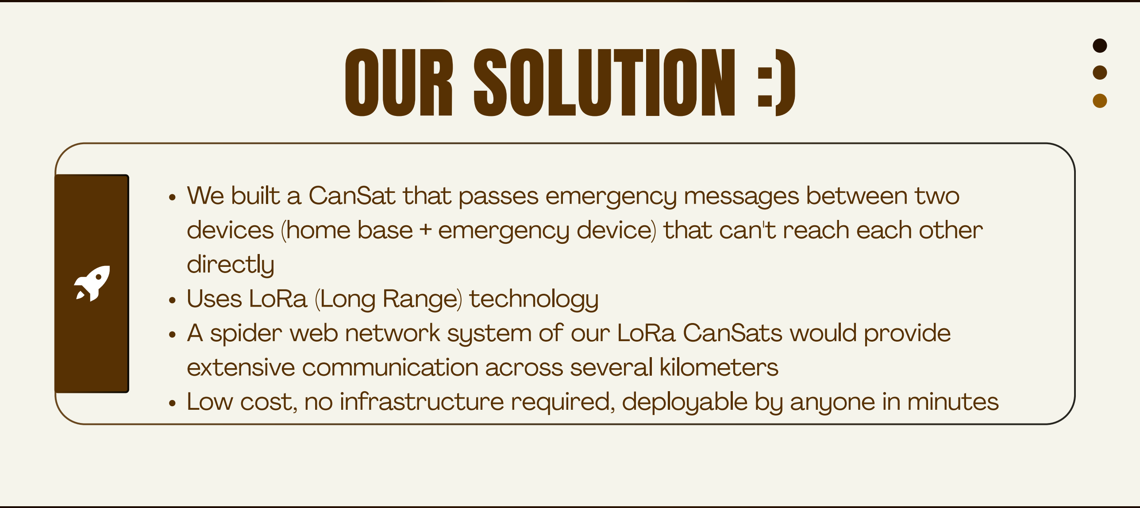
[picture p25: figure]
OUR SOLUTION :); directly Uses LoRa (Long Range) technology

### We built a CanSat that passes emergency messages between two devices (home base + emergency device) that can't reach each other

### A spider web network system of our LoRa CanSats would provide extensive communication across several kilometers Low cost, no infrastructure required, deployable by anyone in minutes

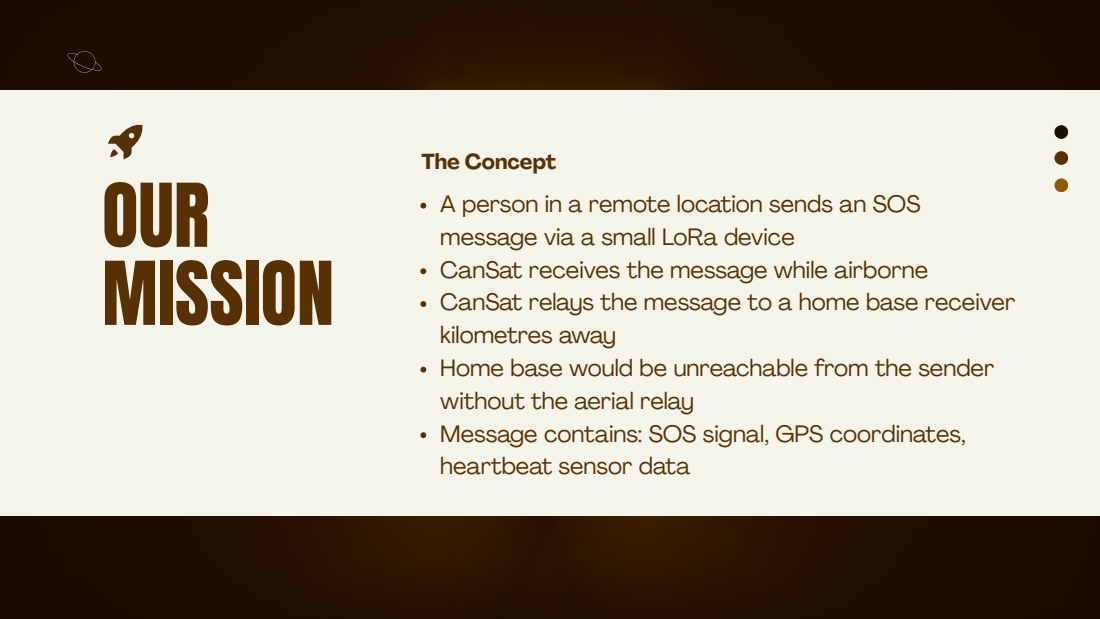
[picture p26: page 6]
OUR MISSION; The Concept

A person in a remote location sends an SOS
message via a small LoRa device
CanSat receives the message while airborne
CanSat relays the message to a home base receiver
kilometres away
Home base would be unreachable from the sender
without the aerial relay
Message contains: SOS signal, GPS coordinates,
heartbeat sensor data

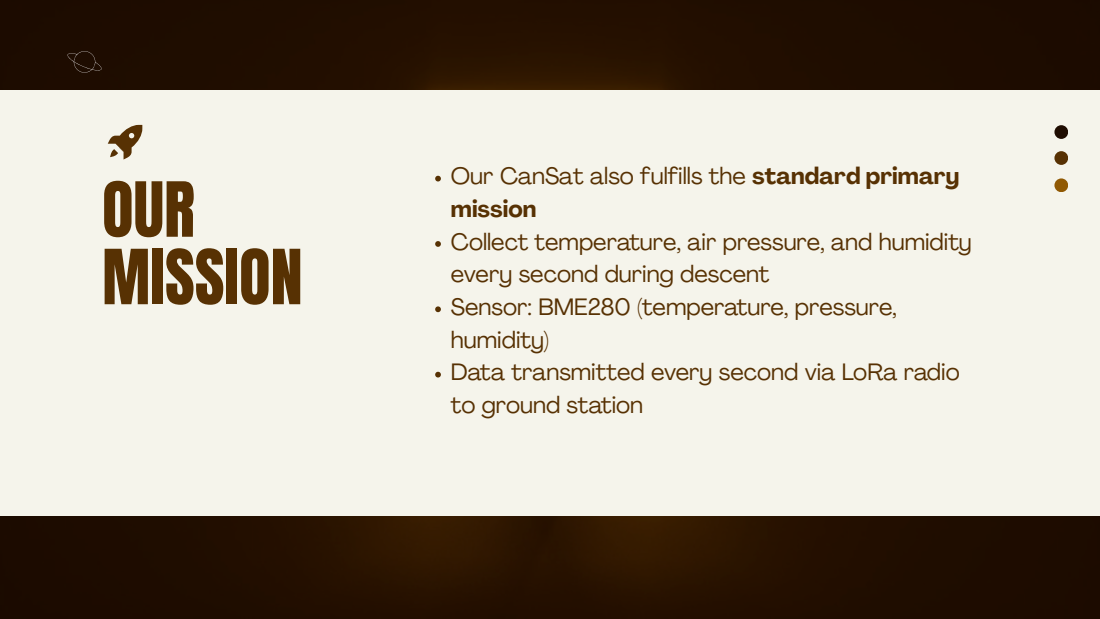
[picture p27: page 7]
OUR MISSION

Our CanSat also fulfills the standard primary
mission
Collect temperature, air pressure, and humidity
every second during descent
Sensor: BME280 (temperature, pressure,
humidity)
Data transmitted every second via LoRa radio
to ground station

# HARDWARE

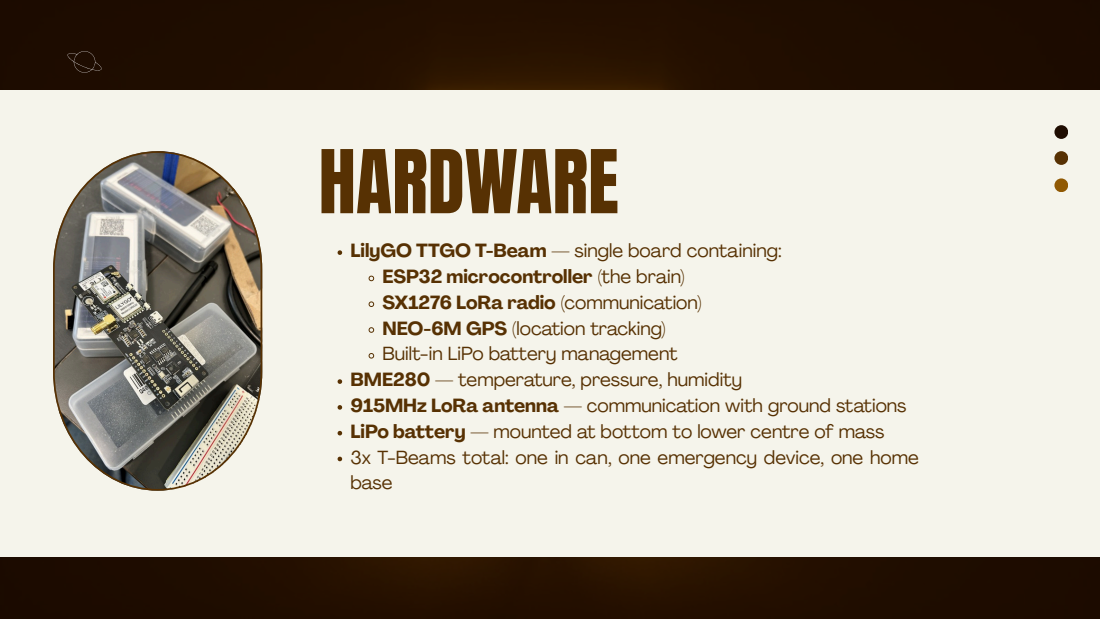
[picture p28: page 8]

LilyGO TTGO T-Beam — single board containing:
ESP32 microcontroller (the brain)
SX1276 LoRa radio (communication)
NEO-6M GPS (location tracking)
Built-in LiPo battery management
BME280 — temperature, pressure, humidity
915MHz LoRa antenna — communication with ground stations
LiPo battery — mounted at bottom to lower centre of mass
3x T-Beams total: one in can, one emergency device, one home
base

# SYSTEM ARCHITECTURE

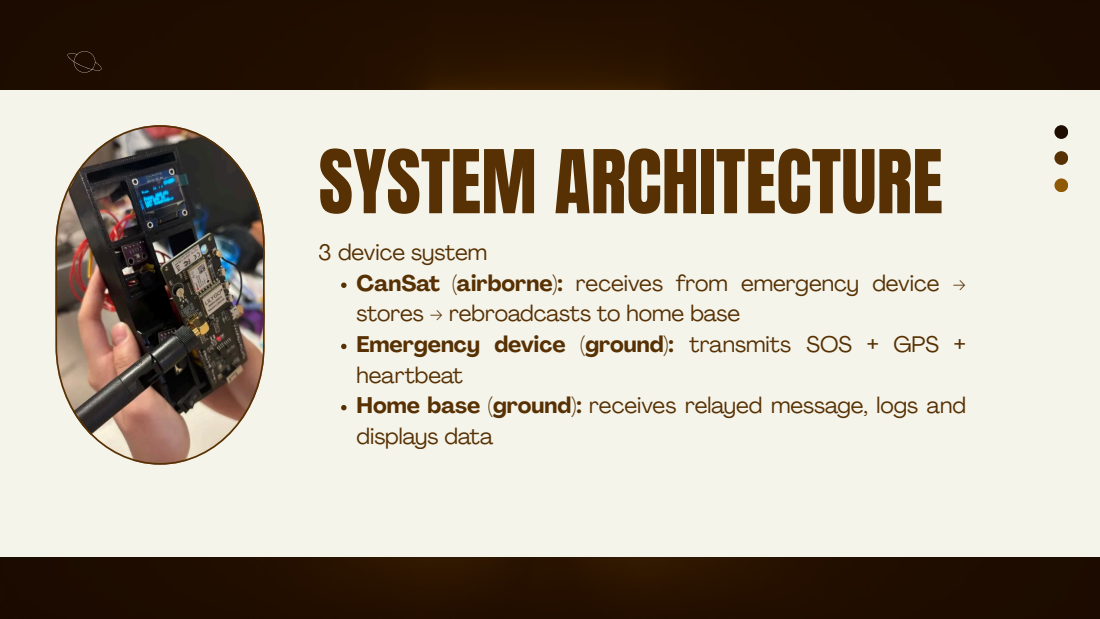
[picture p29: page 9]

3 device system
CanSat (airborne): receives from emergency device →
stores → rebroadcasts to home base
Emergency device (ground): transmits SOS + GPS +
heartbeat
Home base (ground): receives relayed message, logs and
displays data

# FRAME TESTING

Goal: Create a frame able to withstand 20gs of force, fitting all
hardware and remaining under the size limit


Setup: We decided to use PLA with a gyroid infill for distribution of force while remaining light and flexible. After testing with weights and the parachute we decided on 80% infill for top and bottom lids and 20% infill
for the body

Results: Our first 5 versions of testing concluded in many failures but excelled in stability and impact force reduction.

Issues: Most of our failures was due to lack of space. The main issue was fitting the antenna and the wires within the given dimentions. We started with hexagons and pentagons but realized we weren’t benefitting from the full range so we ended back with circles.

# SOS RADIO FRAME

The SOS Radio Frame was built with a few things in mind.
1.Has to be able to fit; Antenna, BME280 sensor, oled screen, heartbeat sensor, buzzer, and LoRa32
2.Must be compact and accessible 3.Must be strong enough to not break under hiking environment.

Version 1
Was too small to fit parts Had incorrect measurments
Printed with 20% Infill PLA

Version 2
Fit everything inside
Was a little oversized
Printed with nylon (stronger)

# PROTOTYPES


Version 2

Version 4

Original Version

Version 3

# FRAME


Top lid

Body

Bottom

ELECTRICAL DESIGN

Three devices:
SOS radio device
CanSat
Ground Station

# SOS RADIO DEVICE WIRINING

3.3V

## OLED screen (SDA=21, SCL=22)

### BME 280 (SDA=21, SCL=22, addr 0x76/0x77)

## MAX30102 (SDA=21, SCL=22)

## GND

## OLED BME280 MAX30102

## Buzzer (+ leg to 5V)

SOS Button (other leg → GPIO 2, INPUT _

PULLUP)

# CANSAT WIRINING


3.3V

BME280 (SDA=21, SCL=22, addr 0x76/0x77
+ Leg LED

# GND

### BME280

### (-) Leg LED

Power Switch (Other leg → GPIO 32)

# SOS DEVICE FEATURE


OLED screen
Heartbeat sensor (MAX 30102)
Buzzer
BME280
GPS (NEO-6M)
SOS Button
Power switch

# SOS DEVICE FEATURE


OLED screen displays BME280 data (Altitude, Humidity,
Pressure, Temperature), location, and heartbeat
When finger is detected on the heartbeat sensor, OLED
screen displays your heartbeat (BPM)
Double click SOS button to send SOS message to CanSat
After receiving ACK from CanSat, OLED screen shows the
message send successfully

# COMMUNICATION LOGIC


LoRa device cannot receive and send data at the same time
CanSat alternating between receiving (TX) mode and sending
mode (RX)
Sending data every seconds
RX mode in around 0 - 850ms
TX mode in around 850 - 910ms
SOS radio device spam SOS message for 5 seconds
CanSat send ACK to SOS after successfully receiving
message
TX mode (ACK if avaible) 910 - 925ms
GPS, LED
80% of time in RX (ensure SOS data receiving succesfully)

SOFTWARE; Features Temperature/pressure/humidity graphs + data Heartbeat + GPS coordinates + SOS signal; map on time, but we hope to do that for future prototypes

We couldn’t obtain a license for a static

RECOVERY SYSTEM

Circular parachute is our recovery system
Has to withstand 30 Newtons of force, then descend at a
rate of 5-12 m/s
8 strings of polypropylene twine (durable and hard to
tangle) connect the parachite to the CanSat
Parachute made of nylon fabric

PARACHUTE CALCULATIONS

Circular parachute
Circular parachutes have a drag coefficient of around
Plug in values to drag force equation. Estimated terminal
velocity: approximately 5 m/s, can change due to wind

# OUTREACH PROGRAM

Both social media and in person presentations

# SOCIAL MEDIA

What our social media looks like :)

# OUTREACH PROGRAM


1st in person presentation: local community centre (Kerrisdale Community Centre) Class of kids aged 9-12 in a STEM program
Presentation + egg drop

# OUTREACH PROGRAM

2 in person presentation: high school

nd
STEM-focused school club called Experiment Club
Audience very fitting because participants were already interested in engineering Circuit + breadboard activity
Several of our participants expressed interest in the CanSat competition!!


# OUTREACH PROGRAM

3 in person presentation: elementary school

rd
Grade 4 class in Quilchena Elementary Presentation + egg drop


# BUDGET

TESTING PROCESS; STEP 1: Testing Hardware; pressure) Tested GPS location, LoRa com range; STEP 2: Testing 2 way communication; and ground station

Tested BME sensors (temperature, humidity, altitude, air

Attempt to transfer the sensor data between CanSat

STEP 3: Full wiring + Parachute Began wiring everything on a breadboard; fall speed + stability; STEP 4: Soldering + 3 way communication After testing breadboard we soldered the wires together and began testing communication between SOS Radio ⟶ Cansat ⟶ Ground Station

Attatch weights to the parachute to test

Final Assembly After gathering all the parts we put them together and tested the Cansat! This includes finished frame, solder, parachute, and assembling it.

# THANK YOU!

Questions?

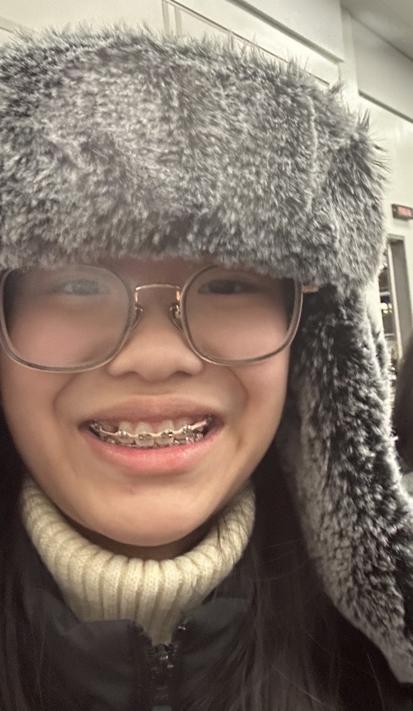
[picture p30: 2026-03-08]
docs/images/Zoey.jpeg

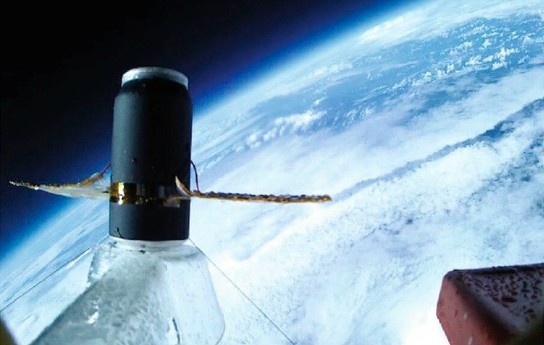
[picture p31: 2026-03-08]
docs/images/cansat.jpg

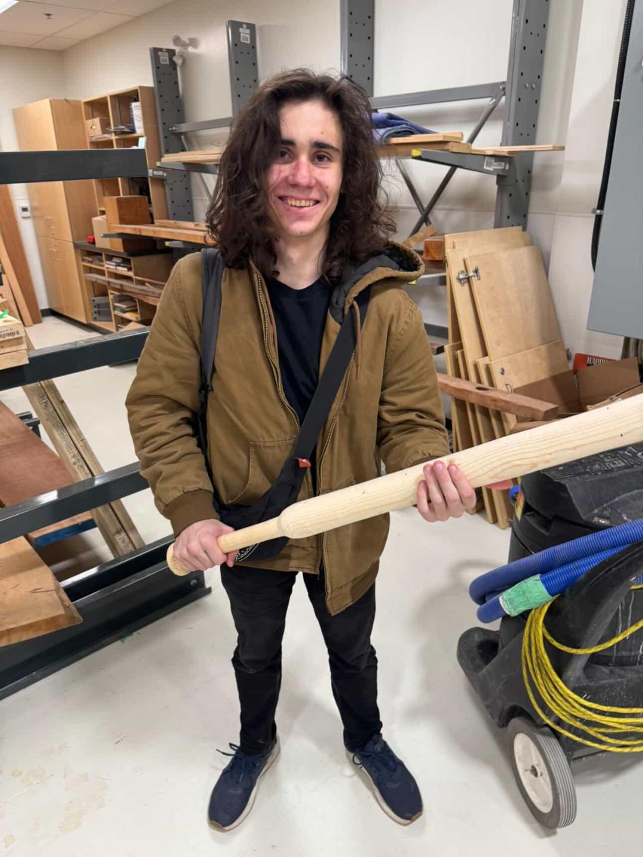
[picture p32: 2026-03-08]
docs/images/Bogdan.jpg

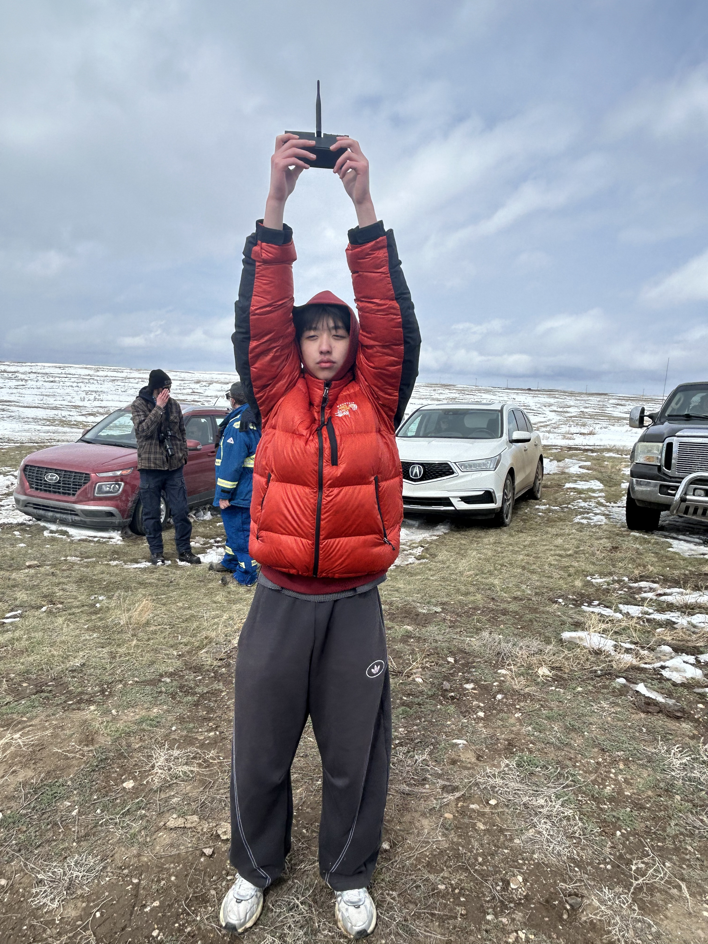
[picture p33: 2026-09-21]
media/GPSlock.jpg

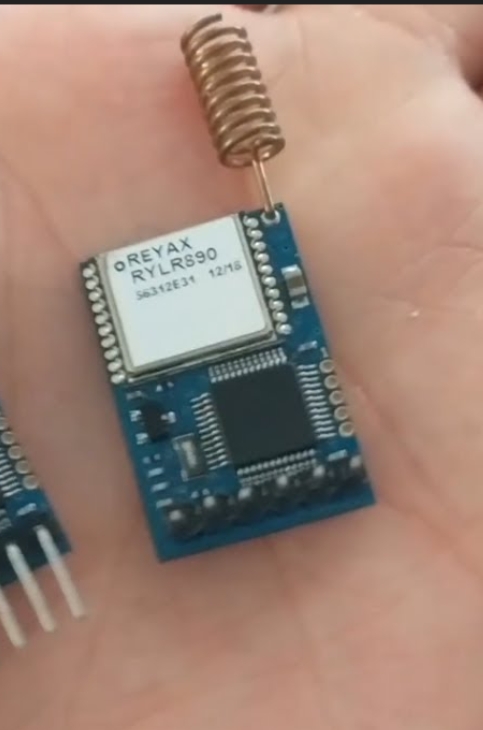
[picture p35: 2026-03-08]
docs/images/loradevice.jpeg

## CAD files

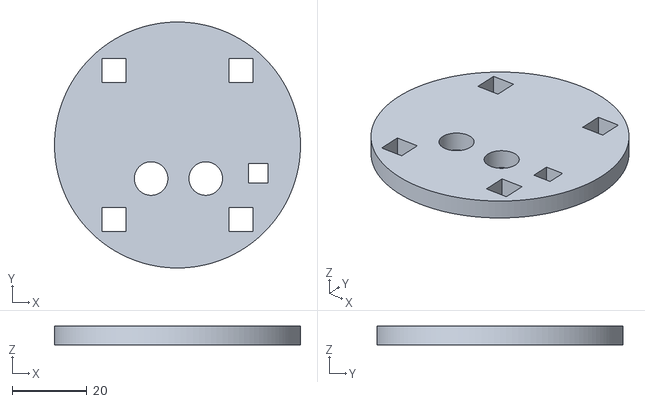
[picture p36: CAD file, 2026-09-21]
cad/CansatV6TopLid-Body.stl
66.0 x 66.0 x 5.00

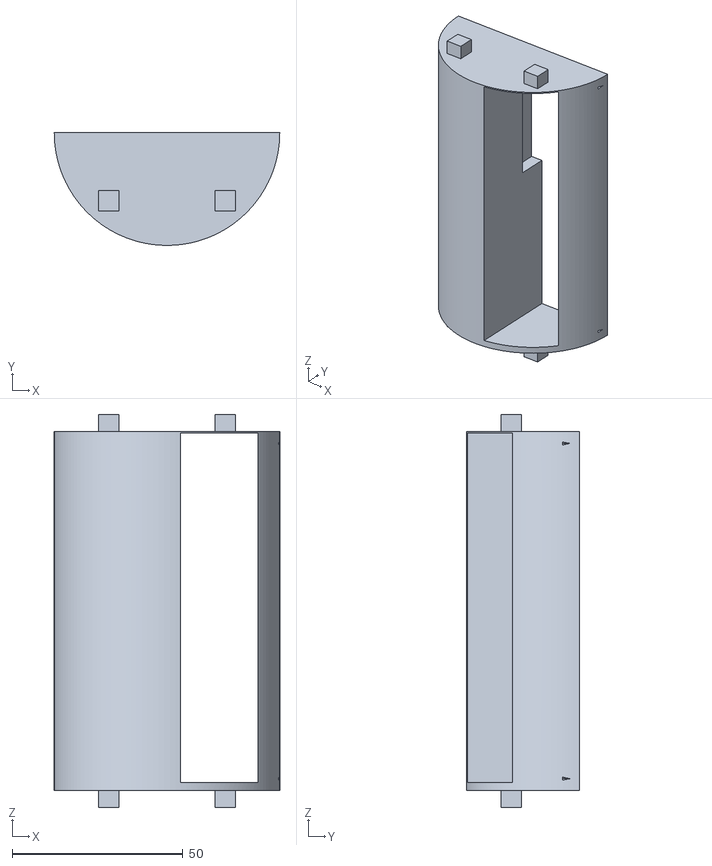
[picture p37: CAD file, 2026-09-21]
cad/CansatLoraBodyV6-Body.stl
66.0 x 33.0 x 115.0

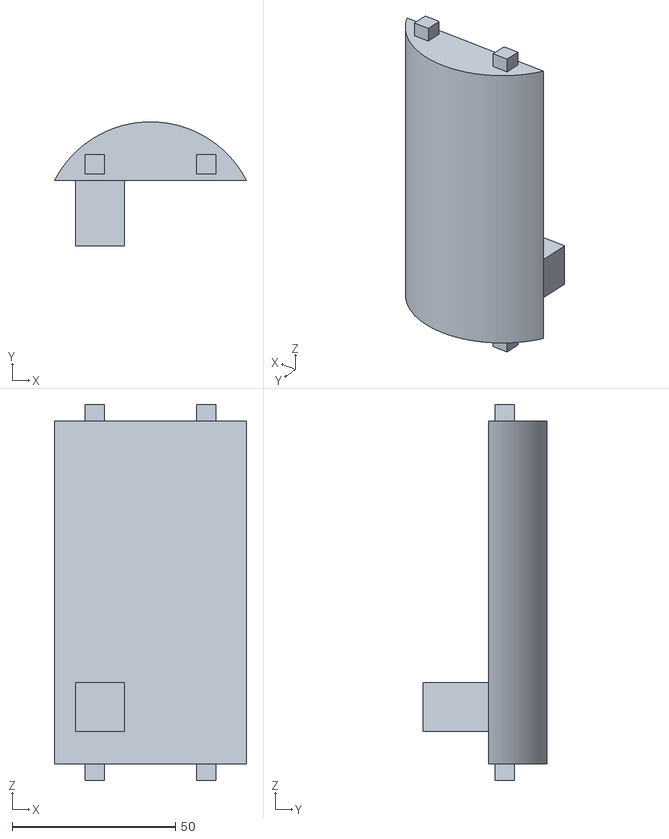
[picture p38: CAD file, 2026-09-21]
cad/CansatV6SecondBody-Body.stl
58.8 x 38.0 x 115.0

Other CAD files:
cad/BottomframeV6-BodyTBottom.stl

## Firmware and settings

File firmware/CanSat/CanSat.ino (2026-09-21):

#include <RadioLib.h>
#include <Wire.h>
#include <SPI.h>
#include <TinyGPSPlus.h>
#include <HardwareSerial.h>
#include <Adafruit_BME280.h>
#include <Adafruit_Sensor.h>
// lora define
#define CS 18
#define DIO0 26
#define reset 4
#define DIO1 33
#define SCK 5
#define MISO 19
#define MOSI 27
// gps define
#define gps_rx 34
#define gps_tx 12
#define gps_baud 9600

#define SDA 21
#define SCL 22
#define led 4
#define AXP_adr 0x34
#define pw_pin 32

#define frq 905.0
#define bandw 250.0
#define spread 7
#define code_rate 5
#define sync_sos 0x34
#define sync_gnd 0xAB

#define frame 1000UL
#define rx_ms 850UL
#define sos_ms 10000UL
#define ack_ms 900UL

#define bms_ms 200
#define led_ms 200

SX1276 radio = new Module(CS, DIO0, reset, DIO1);
Adafruit_BME280 bme;
TinyGPSPlus gps;
HardwareSerial gpsSerial(1);

//definning states
bool bmeReady = false;
float base_pres = 1013.25;
unsigned long ledOnAt = 0;
bool ledOn = false;
unsigned long pac = 0;

//DIO0 interrrupt when a packet arrive
volatile bool receive = false;

float snapTemp = -99;
float snapHum = -99;
float snapPres = -99;
float snapAlt = -99;
unsigned long bme_update = 0;

// sos cache
bool sosReceive = false;
bool sosFresh = false;
unsigned long sos_heart = 0;
unsigned long ack = 0;
String sosBPM = "n";
String sosLat = "n";
String sosLon = "n";
String sosTemp = "n";
String sosHum = "n";

//Axp2101
void axp_w(uint8_t reg, uint8_t val){
  Wire.beginTransmission(AXP_adr);
  Wire.write(reg);
  Wire.write(val);
  Wire.endTransmission();
}
uint8_t axp_r(uint8_t reg){
  Wire.beginTransmission(AXP_adr);
  Wire.write(reg);
  Wire.endTransmission(false);
  Wire.requestFrom(AXP_adr, (uint8_t)1);
  return Wire.available() ? Wire.read() : 0xFF;
}

//led flash
void led_flash(){digitalWrite(led, HIGH); ledOn=true; ledOnAt=millis();}

void updateLED(){
  if(ledOn && millis() - ledOnAt >= led_ms){
    digitalWrite(led, LOW); ledOn = false;
  }
}

//bme update
void bms_snap(){
  if (!bmeReady) return;
  if (millis() - bme_update < bms_ms) return;
  bme_update = millis();
  snapTemp = bme.readTemperature();
  snapHum  = bme.readHumidity();
  snapPres = bme.readPressure()/100.0F;
  snapAlt  = bme.readAltitude(base_pres);
}

void sos_update(){
  if (sosFresh && (millis() - sos_heart > sos_ms)){
    sosFresh = false;
    sosBPM = "n"; sosLat = "n"; sosLon = "n"; sosTemp = "n"; sosHum = "n";
    Serial.println(F("sos data clear"));
  }
}

void sos_cashe(const String& pkt){
  //bpm valid when finger on sensor
  int finIdx = pkt.indexOf("finger:");
  if (finIdx != -1 && pkt.substring(finIdx + 4, finIdx + 5) == "1"){
    int idx = pkt.indexOf("BPM:");
    if (idx != -1){
      int end = pkt.indexOf(",", idx);
      if (end < 0) end = pkt.length();
      sosBPM = pkt.substring(idx + 4, end);
    }else sosBPM = "n";
  } 
  else {
    sosBPM = "n";
  }

  //gps from radio device
  int gpsIdx = pkt.indexOf("GPS:");
  if (gpsIdx != -1 && pkt.substring(gpsIdx + 4, gpsIdx + 5) == "1"){
    int latIdx = pkt.indexOf("Lat:");
    if (latIdx != -1){
      int end = pkt.indexOf(",", latIdx);
      if (end < 0) end = pkt.length();
      sosLat = pkt.substring(latIdx + 4, end);
    }
    int lngIdx = pkt.indexOf("lon:");
    if (lngIdx != -1){
      int end = pkt.indexOf(",", lngIdx);
      if (end < 0) end = pkt.length();
      sosLon = pkt.substring(lngIdx + 4, end);
    }
  } 
  else{
    sosLat = "n";
    sosLon = "n";
  }

  //env data cahse from radio device
  int tIdx = pkt.indexOf(",T:");
  if (tIdx != -1){
    int end = pkt.indexOf(",", tIdx + 1);
    if (end < 0) end = pkt.length();
    sosTemp = pkt.substring(tIdx + 3, end);
  }else sosTemp = "n";

  int hIdx = pkt.indexOf(",H:");
  if (hIdx != -1){
    int end = pkt.indexOf(",", hIdx + 1);
    if (end < 0) end = pkt.length();
    sosHum = pkt.substring(hIdx + 3, end);
  } else sosHum = "n";

  sosReceive = true;
  sosFresh = true;
  sos_heart = millis();

  // Serial.println(F("sos_cashed suscess"));
  // Serial.print(F(" BPM=")); Serial.print(sosBPM);
  // Serial.print(F(" LAT=")); Serial.print(sosLat);
  // Serial.print(F(" LON=")); Serial.print(sosLon);
  // Serial.print(F(" T=")); Serial.print(sosTemp);
  // Serial.print(F(" H=")); Serial.println(sosHum);
}

// telemetry to gnd
void send(){
  pac++;

  String lat = gps.location.isValid() ? String(gps.location.lat(), 6) : "n";
  String lon = gps.location.isValid() ? String(gps.location.lng(), 6) : "n";

  String packet = "cansat";
  packet += "," + String(snapTemp, 1);
  packet += "," + String(snapHum, 1);
  packet += "," + String(snapPres, 1);
  packet += "," + String(snapAlt, 1);
  packet += "," + lat;
  packet += "," + lon;
  packet += ",SEQ:" + String(pac);

  if (sosFresh){
    packet += ",SOS:1";
    packet += ",BPM:" + sosBPM;
    packet += ",SLAT:" + sosLat;
    packet += ",SLON:" + sosLon;
    packet += ",STEMP:" + sosTemp;
    packet += ",SHUM:" + sosHum;
  } 
  else{
    packet += ",SOS:0";
  }

  radio.standby();
  radio.setSyncWord(sync_gnd);
  int state = radio.transmit(packet);

  // Serial.print(F("tx gnd#")); Serial.print(pac);
  // Serial.print(F(" ")); Serial.println(packet);
  // if (state != RADIOLIB_ERR_NONE){
  //   Serial.print(F("tx err ")); Serial.println(state);
  // }
  led_flash();
}

// send ack
void send_ack() {
  if (!sosFresh) return;
  if (millis()-ack < ack_ms) return;

  radio.standby();
  radio.setSyncWord(sync_sos);
  int st = radio.transmit("ack");
  ack = millis();
  Serial.print(F("ack_sos stat=")); Serial.println(st);
}

void waiting_switch(){
  if (digitalRead(pw_pin) == HIGH) return;
  Serial.println(F("switch off"));
  while (digitalRead(pw_pin) == LOW) {delay(100);}
  Serial.println(F("switch on"));
  delay(200);
}

void run_frame() {
  unsigned long frameStart = millis();

  // refresh sensors at frame start
  while (gpsSerial.available()) gps.encode(gpsSerial.read());
  bms_snap();
  sos_update();

  receive = false;
  radio.standby();
  radio.setSyncWord(sync_sos);
  radio.startReceive();

  while (millis()-frameStart < rx_ms){
    while (gpsSerial.available()) gps.encode(gpsSerial.read());

    if (receive){
      receive = false;
      
      String incoming;
      int rxState = radio.readData(incoming);
      
      if (rxState == RADIOLIB_ERR_NONE && incoming.startsWith("SOS")){
        Serial.print(F("rx sos")); Serial.println(incoming);
        sos_cashe(incoming);
      } 
      else{
        Serial.print(F("ex err code:")); Serial.println(rxState);
      }
      radio.startReceive();
    }
    delay(2);
  }
  send();

  #define tx_ms 50UL
  if (millis()-frameStart < (frame - tx_ms)){
    send_ack();
  } 
  else{
    Serial.println(F("ack slipped"));
  }
// 1 sec boundry
  while (millis() - frameStart < frame){
    updateLED();
    while (gpsSerial.available()) gps.encode(gpsSerial.read());
    delay(1);
  }
}

#if defined(ESP8266) || defined(ESP32)
  ICACHE_RAM_ATTR
#endif
void setFlag(){
  receive = true;
}

void setup(){
  Serial.begin(115200);
  pinMode(pw_pin, INPUT);
  delay(500);
  Serial.println(F("CatSat starting"));

  pinMode(led, OUTPUT);
  digitalWrite(led, LOW);
  Wire.begin(SDA, SCL);

  //axp power rail
  axp_w(0x92, (1800 - 500)/100);
  axp_w(0x90, axp_r(0x90) | 0x20);
  axp_w(0x93, (3300-500)/100);
  axp_w(0x90, axp_r(0x90) | 0x40);
  axp_w(0x94, (3300 - 500)/100);
  axp_w(0x90, axp_r(0x90)|0x80);
  delay(500);
  Serial.println(F("axp set"));

  gpsSerial.begin(gps_baud, SERIAL_8N1, gps_rx, gps_tx);
  Serial.println(F("gps locking"));

  if (bme.begin(0x76) || bme.begin(0x77)){
    bmeReady = true;
    bme.setSampling(
      Adafruit_BME280::MODE_NORMAL,
      Adafruit_BME280::SAMPLING_X2,
      Adafruit_BME280::SAMPLING_X16,
      Adafruit_BME280::SAMPLING_X1,
      Adafruit_BME280::FILTER_X16,
      Adafruit_BME280::STANDBY_MS_500
    );
    base_pres = bme.readPressure()/100.0F;
    snapTemp = bme.readTemperature();
    snapHum  = bme.readHumidity();
    snapPres = bme.readPressure()/100.0F;
    snapAlt  = bme.readAltitude(base_pres);
    bme_update = millis();
    Serial.print(F("bme280 set base: "));
    Serial.print(base_pres); Serial.println(F(" hPa"));
  } 
  else{
    Serial.println(F("bme not found"));
  }

  SPI.begin(SCK, MISO, MOSI, CS);
  int state = radio.begin(
    frq, bandw,
    spread, code_rate,
    sync_sos
  );
  if (state == RADIOLIB_ERR_NONE){
    Serial.println(F("LoRa set"));
    radio.setDio0Action(setFlag, RISING);
  } 
  else{
    Serial.print(F("LoRa fail")); Serial.println(state);
    while (true);
  }

  digitalWrite(led, HIGH);
  Serial.println(F("CanSat set"));
}

void loop() {
  waiting_switch();
  updateLED();
  run_frame();
}

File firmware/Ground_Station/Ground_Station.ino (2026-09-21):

#include <RadioLib.h>
#include <Wire.h>
#include <SPI.h>

#define cs 18
#define DIO0 26
#define reset 4
#define DIO1 33
#define sck 5
#define MISO 19
#define MOSI 27
#define SDA 21
#define SCL 22
#define led 4
#define axp_adr 0x34

#define frq 905.0
#define band_w 250.0
#define spread 7
#define c_rate 5
#define sync_gnd 0xAB

#define led_flash 300

SX1276 radio = new Module(cs, DIO0, reset, DIO1);
// state
unsigned long ledOnAt = 0;
bool ledOn = false;

// axp
void axp_w(uint8_t reg, uint8_t val){
  Wire.beginTransmission(axp_adr);
  Wire.write(reg); Wire.write(val);
  Wire.endTransmission();
}
uint8_t axp_r(uint8_t reg) {
  Wire.beginTransmission(axp_adr);
  Wire.write(reg); Wire.endTransmission(false);
  Wire.requestFrom(axp_adr, (uint8_t)1);
  return Wire.available() ? Wire.read() : 0xFF;
}


// led
void flashLED() {digitalWrite(led, HIGH); ledOn = true; ledOnAt = millis();}

void updateLED(){
  if (ledOn && millis() - ledOnAt >= led_flash){
    digitalWrite(led, LOW); ledOn = false;
  }
}

String extract(const String& pkt, const String& key){
  int idx = pkt.indexOf(key);
  if (idx == -1) return "n";
  int start = idx + key.length();
  int end = pkt.indexOf(",", start);
  if (end == -1) end = pkt.length();
  return pkt.substring(start, end);
}


void packSat(const String& packet){
  String fields[7];
  int fieldIdx = 0;
  String token = "";

  for (int i = 0; i <= (int)packet.length() && fieldIdx < 7; i++){
    char c = (i < (int)packet.length()) ? packet[i] : ',';
    if (c == ','){
      fields[fieldIdx++] = token;
      token = "";
    } else token += c;
  }
  
  
  // fields[0]="cansat",[1]=temp,[2]=hum,[3]=pres,[4]=alt,[5]=lat,[6]=lon
  Serial.print(F("cansat,"));
  Serial.print(fields[1]); Serial.print(F(",")); // temp
  Serial.print(fields[2]); Serial.print(F(",")); // humidity
  Serial.print(fields[3]); Serial.print(F(",")); // pressure
  Serial.print(fields[4]); Serial.print(F(",")); // altitude
  Serial.print(fields[5]); Serial.print(F(",")); // lat
  Serial.println(fields[6]); // lon

  String sosFlag = extract(packet, "SOS:");
  if (sosFlag == "1"){
    String bpm = extract(packet, "BPM:");
    String slat = extract(packet, "s_lat:");
    String slon = extract(packet, "s_lon:");
    String stemp = extract(packet, "s_temp:");
    String shum = extract(packet, "s_hum:");

    Serial.print(F("sos_info,"));
    Serial.print(fields[1]); Serial.print(F(",")); // cansat temp
    Serial.print(fields[2]); Serial.print(F(",")); // cansat hum
    Serial.print(fields[3]); Serial.print(F(",")); // cansat pres
    Serial.print(fields[4]); Serial.print(F(","));// cansat alt
    Serial.print(fields[5]); Serial.print(F(",")); // cansat lat
    Serial.print(fields[6]); Serial.print(F(",")); // cansat lon
    Serial.print(bpm); Serial.print(F(",")); // sos BPM
    Serial.print(slat); Serial.print(F(",")); // sos lat
    Serial.print(slon); Serial.print(F(",")); // sos lon
    Serial.print(stemp); Serial.print(F(","));// sos temp
    Serial.println(shum); // sos hum
  }
}

volatile bool receivedFlag = false;

#if defined(ESP8266) || defined(ESP32)
  ICACHE_RAM_ATTR
#endif
void setFlag() {receivedFlag = true;}

void setup() {
  Serial.begin(115200);
  delay(500);

  pinMode(led, OUTPUT);
  digitalWrite(led, LOW);

  Wire.begin(SDA, SCL);

  axp_w(0x93,(3300 - 500)/100);
  axp_w(0x90, axp_r(0x90) | 0x40);
  delay(500);

  SPI.begin(sck, MISO, MOSI,cs);
  int state = radio.begin(
    frq, band_w,
    spread, c_rate,
    sync_gnd
  );

  if (state == RADIOLIB_ERR_NONE){
    digitalWrite(led, HIGH);
    radio.setDio0Action(setFlag, RISING);
    radio.startReceive();
    Serial.println(F("GND Set"));
    Serial.println(F("Porting with Cansat"));
  } 
  else{
    Serial.print(F("GND fail")); Serial.println(state);
    while (true);
  }
}

void loop() {
  updateLED();

  if (!receivedFlag) return;
  receivedFlag = false;

  String incoming;
  int state = radio.readData(incoming);

  if (state == RADIOLIB_ERR_NONE) {
    flashLED();
    if (incoming.startsWith("cansat")){
      packSat(incoming);
    }
  } 
  else{
    Serial.print(F("rx err")); Serial.println(state);
  }
  radio.startReceive();
}
